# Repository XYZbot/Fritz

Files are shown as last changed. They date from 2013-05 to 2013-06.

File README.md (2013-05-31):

# Fritz : a robotic puppet

Fritz is an animatronic puppet that is controlled by an Arduino microcontroller. Fritz 
was created to provide an inexpensive introduction into robotics that is both entertaining, creative 
and educational. With an open source directive, Fritz is accompanied by a PC application to 
provide you with an easy to use interface in customizing and interacting with the project mechanics.

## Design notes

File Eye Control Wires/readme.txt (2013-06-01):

Open source release 1.0

Date: 5/31/2013

This directory contains .pdf files that show mechanical drawings
for how to make the control wires for Fritz.

These parts can be made using 0.032" diameter music wire.  Bends
can be made by hand using needle nose pliars.  A digital caliper
will be highly useful in making measurements prior to making bends.

There are 2 each of the horizontal and vertical wires.  There
are 4 each of the eyelid wires.

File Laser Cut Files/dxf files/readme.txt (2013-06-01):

Open source release 1.0

Date: 5/31/2013

This directory contains .dxf format files exported from solidworks.
These files can be used to import into a program to do laser cutting
of the parts for Fritz.

Note that parts that are repeated (occur more than once in a Fritz)
have a "_2x" in the filename to signal to you that you need more 
than one.

www.xyzbot.com

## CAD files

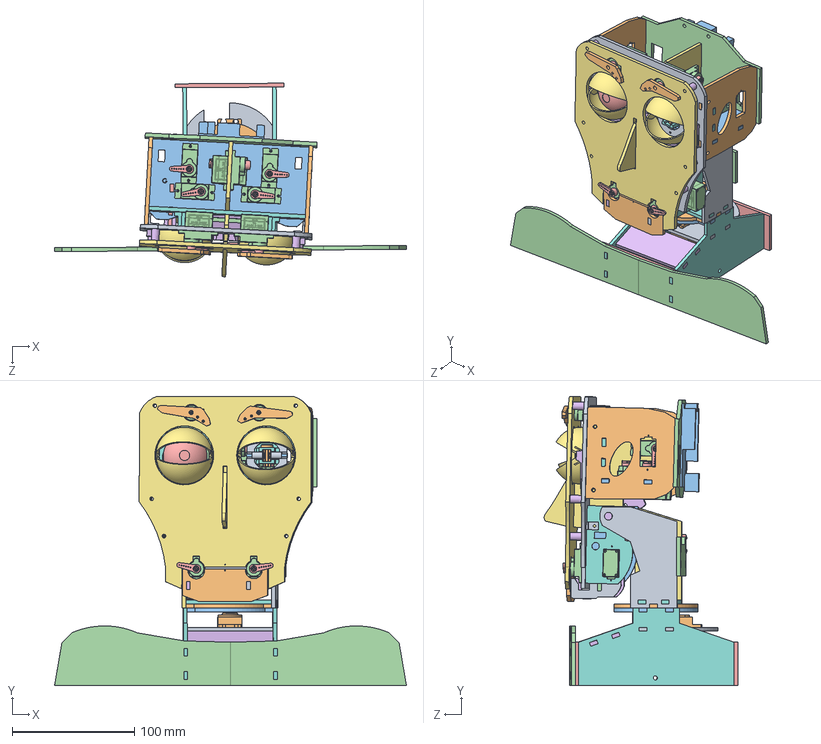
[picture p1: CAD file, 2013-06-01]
Solidworks Files/AssemblyFull.SLDASM
287.8 x 236.6 x 158.4 mm
faceFrameBack
skullbox_side x 2
skullbox_bottom
SG90 BODY x 11
SG90 ARM x 11
spacer_#6thread_3_4trlong x 6
faceFrameFront
skullBoxMandible
jawbone3
jawFront
skullBoxMandibleRight
jawCrossBeam
mandibleBack
jawboneRight
skullBoxNosePanel
skullbox_firewall
angleBracket_4_40screwThread x 6
eyebrow x 2
unoKitBoard
skullbox_back
gearLargeB
gearLargeNoTabs x 2
spacerNeckTilt
eyeBracket_straightPull x 2
eyeRing_straightPull x 2
clevisPin_cored x 2
eyeXAxisRod x 2
spacer_1_4trlong x 4
eye
eyeLidMount_B x 2
eyelidA x 4
rotateBaseSides x 2
rotateBaseServoPlate
Standard ServoB x 2
thrustBearingBottom
shoulderFront x 2
chestWall x 2
neckCover
neckTiltColumn
neckTiltColumnBottom
neckTiltColumnLeft
thrustBearingTop
servoHorn4Arm_standardSize
neckTiltColumnBack
gearSmall
tiltAxle

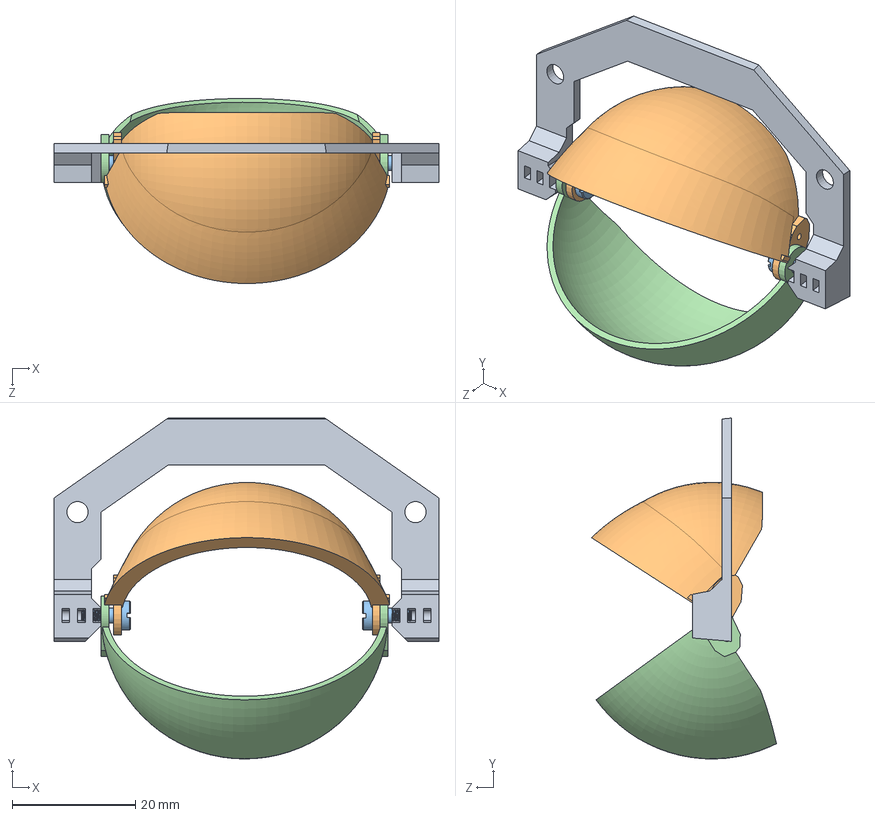
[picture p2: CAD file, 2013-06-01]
Solidworks Files/Assembly_EyeLid.SLDASM
62.4 x 55.2 x 30.0 mm
eyeLidMount_B
eyelidBottomD
shoulderScrew_2_56_1_8ths_shoulderLngth x 2
eyelidTopB

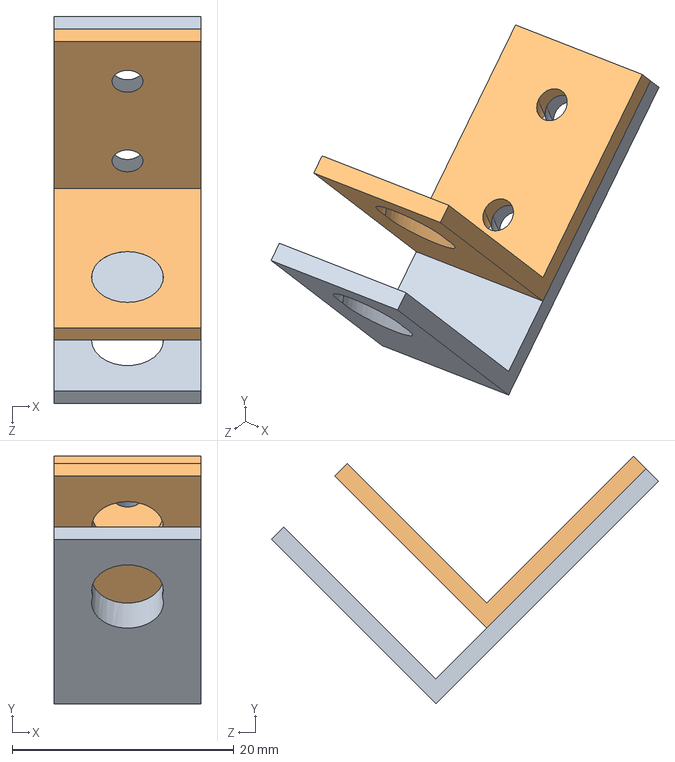
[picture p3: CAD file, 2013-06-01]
Solidworks Files/Assembly_eyeBracket.SLDASM
13.2 x 22.3 x 34.9 mm
eyeBracketHalf2
eyeBracketHalf1

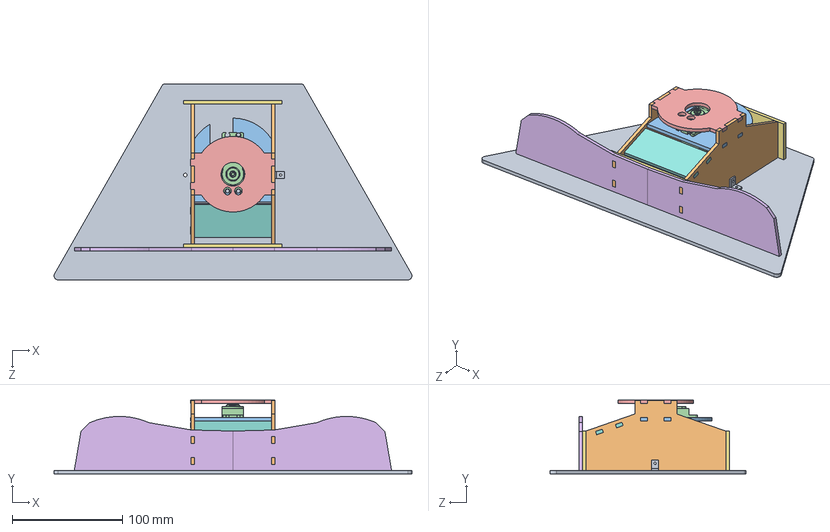
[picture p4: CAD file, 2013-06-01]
Solidworks Files/assemblyBaseToBasePlate.SLDASM
324.7 x 66.7 x 177.8 mm
basePlate
rotateBaseSides x 2
rotateBaseServoPlate
Standard ServoB
thrustBearingBottom
shoulderFront x 2
chestWall x 2
neckCover
angleBracket_4_40screwThread

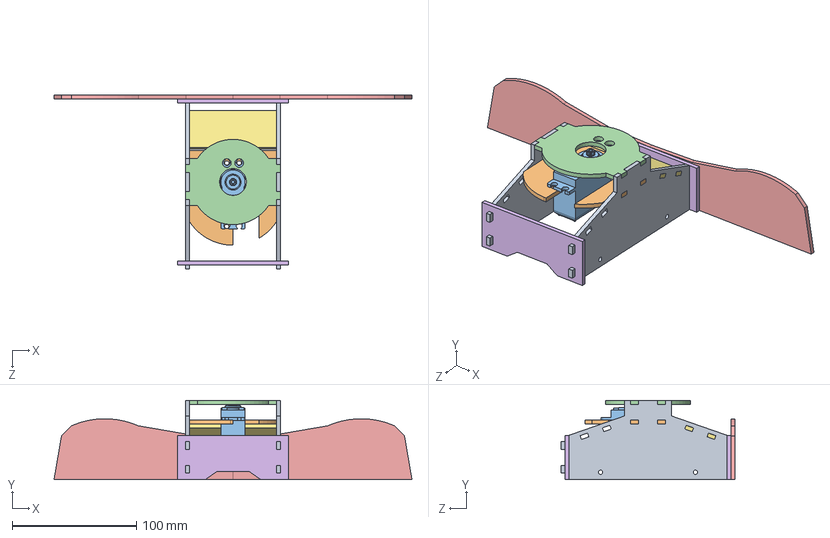
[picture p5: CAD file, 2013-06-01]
Solidworks Files/assemblyRotateBase.SLDASM
287.8 x 63.6 x 139.7 mm
rotateBaseSides x 2
rotateBaseServoPlate
Standard ServoB
thrustBearingBottom
shoulderFront x 2
chestWall x 2
neckCover

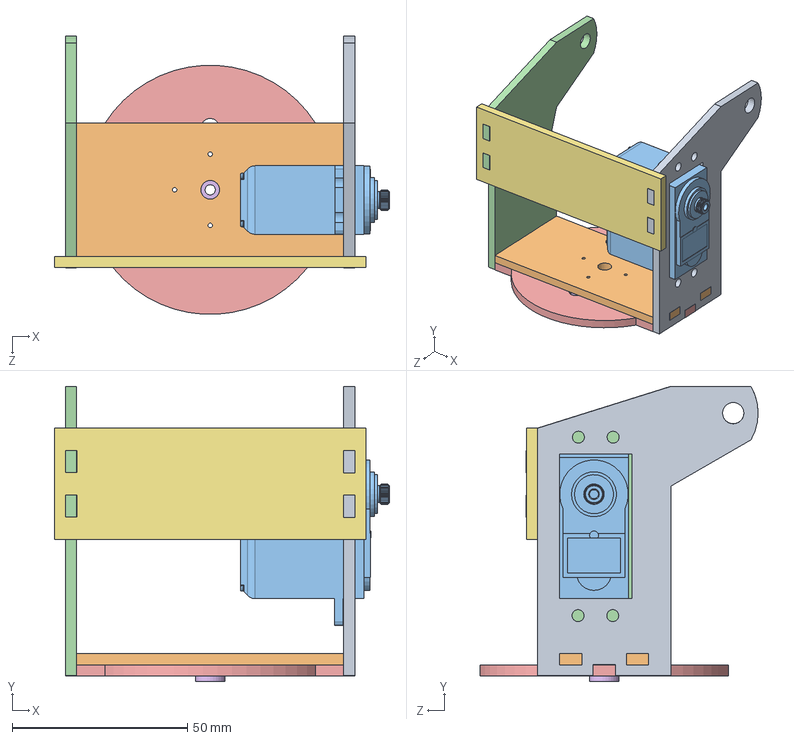
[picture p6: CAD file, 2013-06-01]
Solidworks Files/AssemblyNeckTiltColumn.SLDASM
95.6 x 84.3 x 79.4 mm
neckTiltColumn
neckTiltColumnBottom
Standard ServoB
neckTiltColumnLeft
thrustBearingTop
servoHorn4Arm_standardSize
neckTiltColumnBack

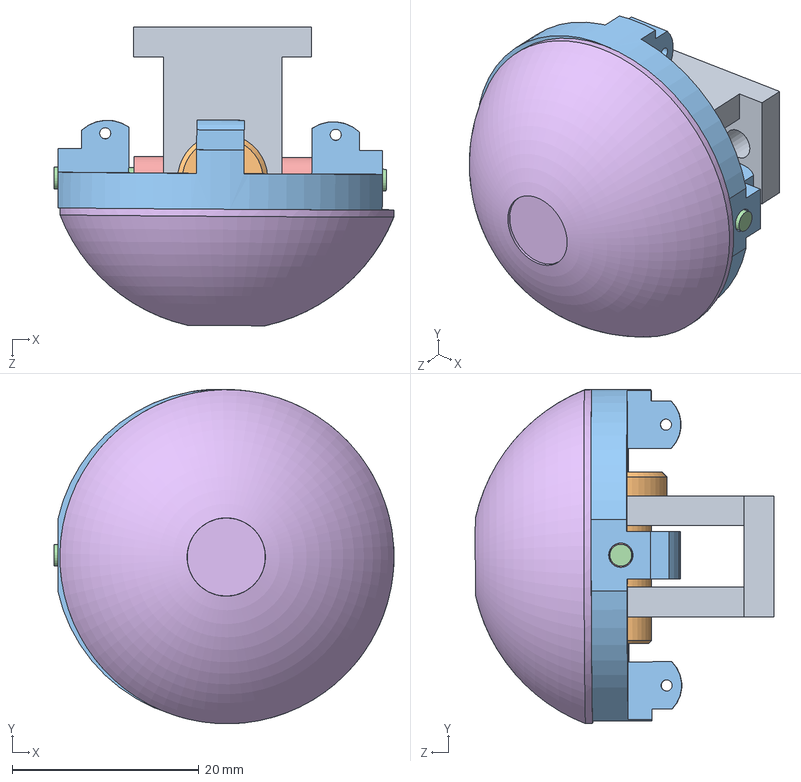
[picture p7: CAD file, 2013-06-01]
Solidworks Files/AssemblyEye.SLDASM
36.4 x 35.8 x 32.0 mm
uBracket
clevis_pin
eyeRingr4
eyeXAxisRod
spacer_1_4trlong x 2
eye

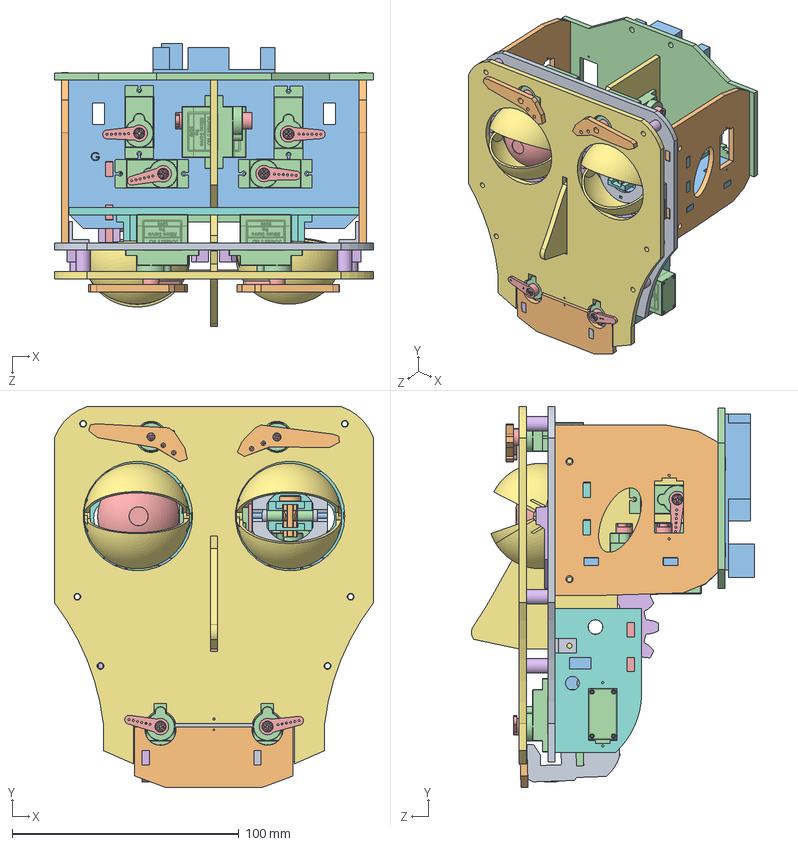
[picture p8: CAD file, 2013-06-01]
Solidworks Files/Assembly_skullbox.SLDASM
140.7 x 167.9 x 124.8 mm
faceFrameBack
skullbox_side x 2
skullbox_bottom
SG90 BODY x 11
SG90 ARM x 11
spacer_#6thread_3_4trlong x 6
faceFrameFront
skullBoxMandible
jawbone3
jawFront
skullBoxMandibleRight
jawCrossBeam
mandibleBack
jawboneRight
skullBoxNosePanel
skullbox_firewall
angleBracket_4_40screwThread x 6
eyebrow x 2
unoKitBoard
skullbox_back
gearLargeB
gearLargeNoTabs x 2
spacerNeckTilt
eyeBracket_straightPull x 2
eyeRing_straightPull x 2
clevisPin_cored x 2
eyeXAxisRod x 2
spacer_1_4trlong x 4
eye
eyeLidMount_B x 2
eyelidA x 4

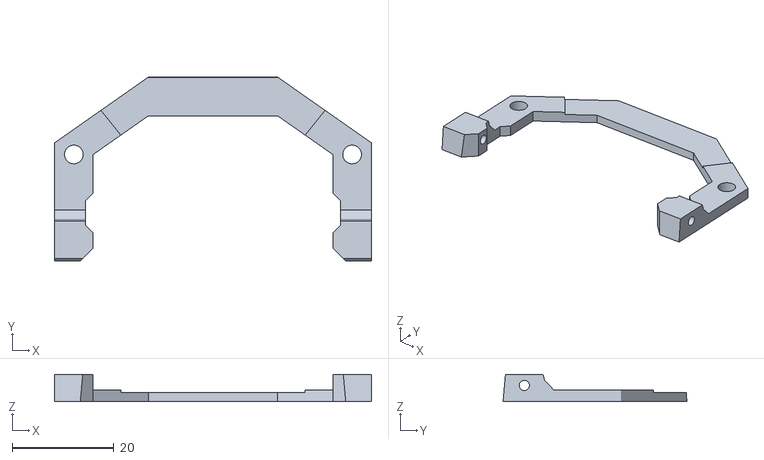
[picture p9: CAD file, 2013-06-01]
3D Printer Files/stl files/eyeLidMount_B.STL
62.4 x 36.2 x 5.33

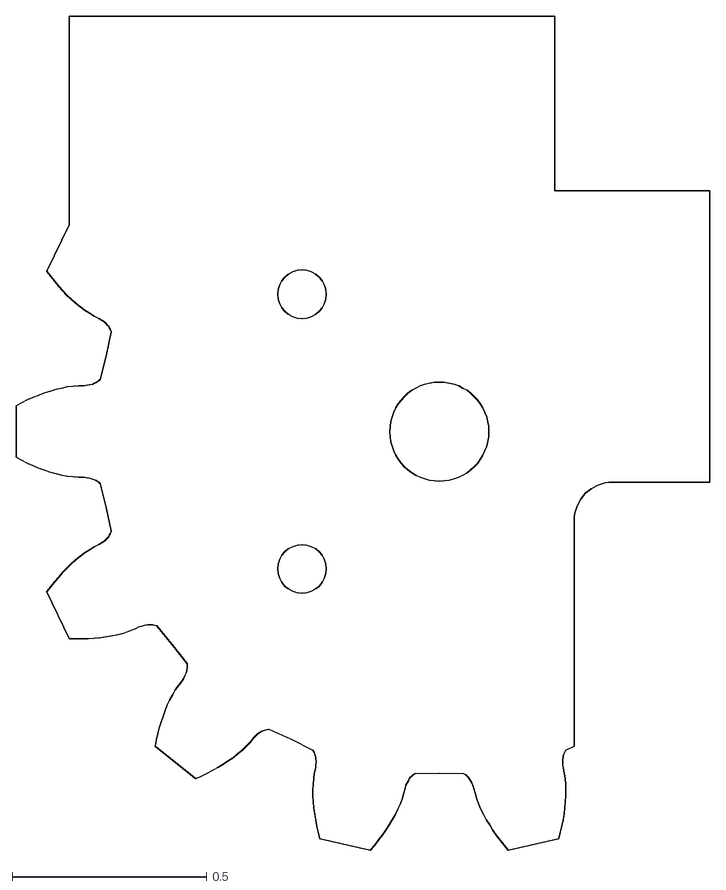
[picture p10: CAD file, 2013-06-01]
Laser Cut Files/dxf files/gearLargeNoTabs.DXF
1.79 x 2.15

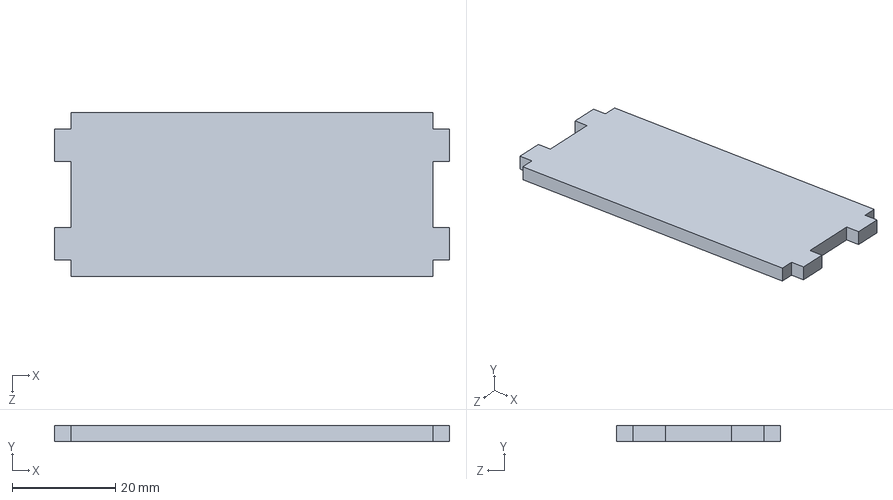
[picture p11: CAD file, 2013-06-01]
Solidworks Files/neckCover.SLDPRT
76.6 x 3.17 x 31.8 mm

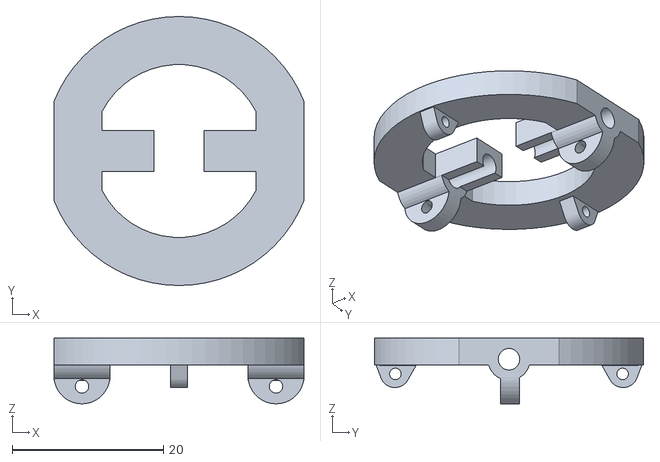
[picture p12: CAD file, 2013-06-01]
3D Printer Files/stl files/eyeRing_3D_rF.STL
33.0 x 35.6 x 8.70

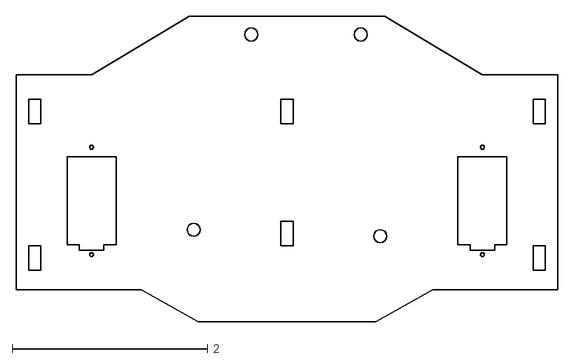
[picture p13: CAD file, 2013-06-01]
Laser Cut Files/dxf files/skullbox_back.DXF
5.54 x 3.13

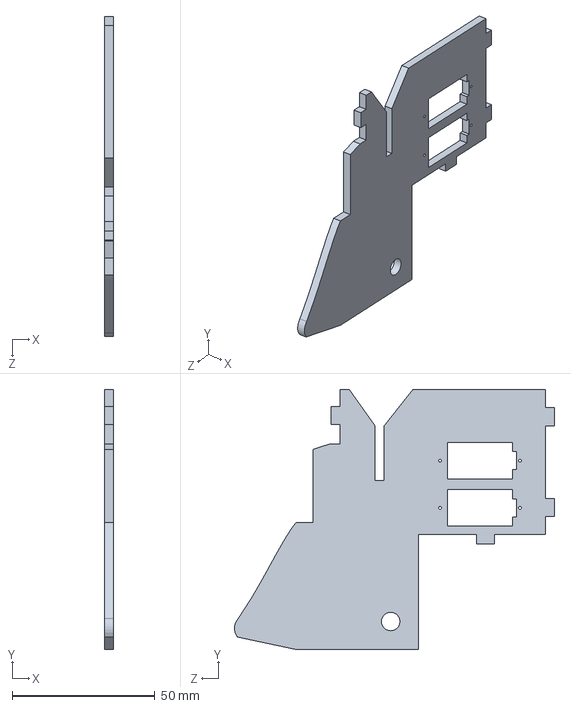
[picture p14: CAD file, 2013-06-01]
Solidworks Files/skullBoxNosePanel.SLDPRT
3.17 x 90.9 x 112.0 mm

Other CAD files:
3D Printer Files/stl files/eyelid3d_wButtress.STL
Laser Cut Files/dxf files/thrustBearingTop.DXF
Solidworks Files/neckRotateServoPlate.SLDPRT
3D Printer Files/stl files/eye bracket 3D-C.STL
3D Printer Files/stl files/clevisPin_3DPrint_B.STL
3D Printer Files/stl files/eyelid3DPrint.STL
Laser Cut Files/dxf files/basePlate.DXF
Laser Cut Files/dxf files/chestWall.DXF
Laser Cut Files/dxf files/eyebrow.DXF
Laser Cut Files/dxf files/faceFrameBack.DXF
Laser Cut Files/dxf files/faceFrameFront.DXF
Laser Cut Files/dxf files/faceFrameFront_devilHead.DXF
Laser Cut Files/dxf files/gearLargeB_2X.DXF
Laser Cut Files/dxf files/gearSmall.DXF
Laser Cut Files/dxf files/gearSmallForAcrylic1_8th.DXF
Laser Cut Files/dxf files/jawCrossBeam.DXF
Laser Cut Files/dxf files/jawFront.DXF
Laser Cut Files/dxf files/jawbone3.DXF
Laser Cut Files/dxf files/jawboneRight.DXF
Laser Cut Files/dxf files/mandibleBack.DXF
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

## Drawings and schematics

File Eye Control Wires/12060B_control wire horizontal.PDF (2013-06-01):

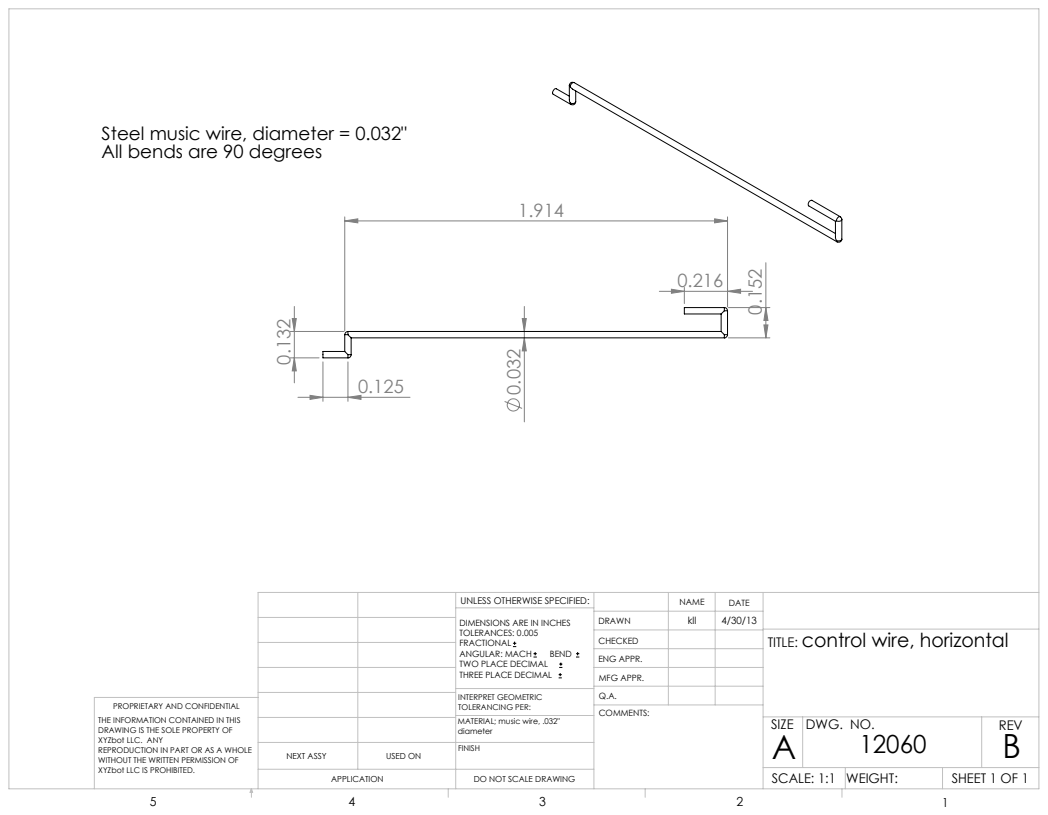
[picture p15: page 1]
SHEET 1 OF 1; SCALE: 1:1 WEIGHT:; DWG. NO.; REV; MFG APPR.; ENG APPR.; ANGULAR: MACH; BEND; NEXT ASSY; USED ON

Steel music wire, diameter = 0.032"
All bends are 90 degrees

UNLESS OTHERWISE SPECIFIED:

DIMENSIONS ARE IN INCHES
TOLERANCES: 0.005
FRACTIONAL
TWO PLACE DECIMAL
THREE PLACE DECIMAL

TITLE: control wire, horizontal

INTERPRET GEOMETRIC
TOLERANCING PER:
MATERIAL; music wire, .032"
diameter
FINISH

PROPRIETARY AND CONFIDENTIAL
THE INFORMATION CONTAINED IN THIS
DRAWING IS THE SOLE PROPERTY OF
XYZbot LLC. ANY
REPRODUCTION IN PART OR AS A WHOLE
WITHOUT THE WRITTEN PERMISSION OF
XYZbot LLC IS PROHIBITED.

DO NOT SCALE DRAWING

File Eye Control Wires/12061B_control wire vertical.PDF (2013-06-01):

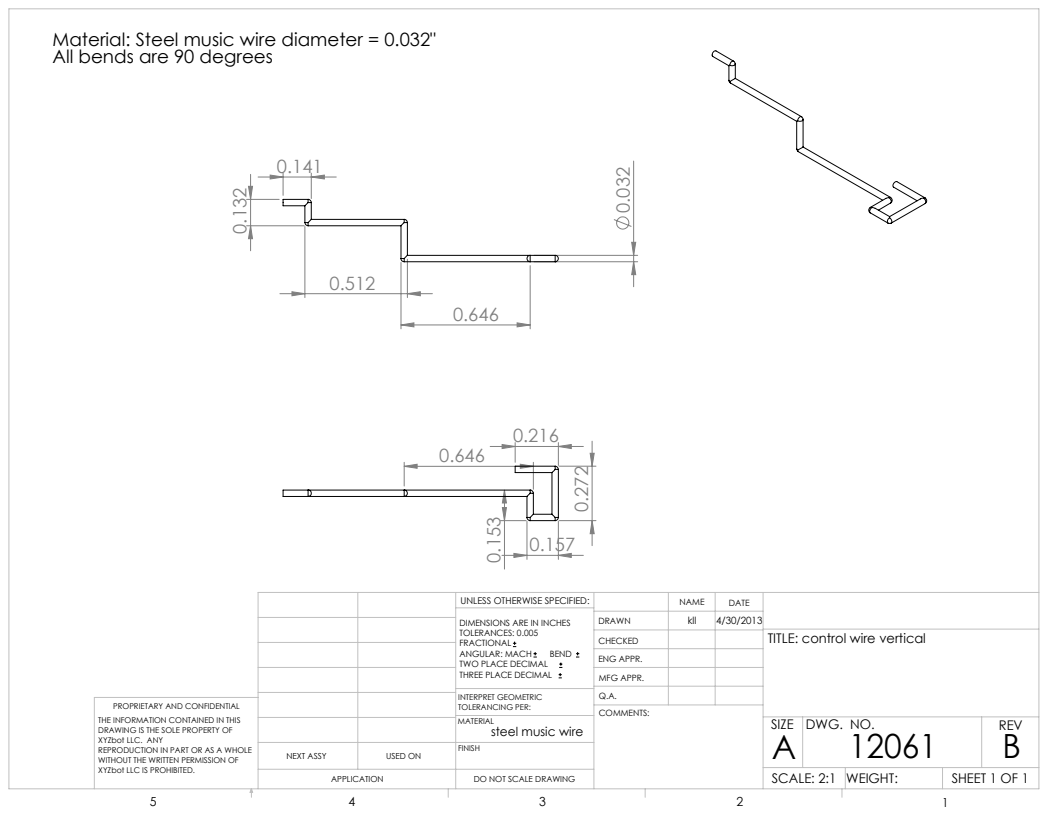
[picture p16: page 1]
SHEET 1 OF 1; SCALE: 2:1 WEIGHT:; DWG. NO.; REV; MFG APPR.; ENG APPR.; ANGULAR: MACH; BEND; NEXT ASSY; USED ON

Material: Steel music wire diameter = 0.032"
All bends are 90 degrees

UNLESS OTHERWISE SPECIFIED:

DIMENSIONS ARE IN INCHES
TOLERANCES: 0.005
FRACTIONAL
TWO PLACE DECIMAL
THREE PLACE DECIMAL

TITLE: control wire vertical

INTERPRET GEOMETRIC
TOLERANCING PER:
MATERIAL
steel music wire
FINISH

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

DO NOT SCALE DRAWING

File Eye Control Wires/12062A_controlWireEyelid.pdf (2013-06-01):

# Material: steel music wire, diameter = 0.032"

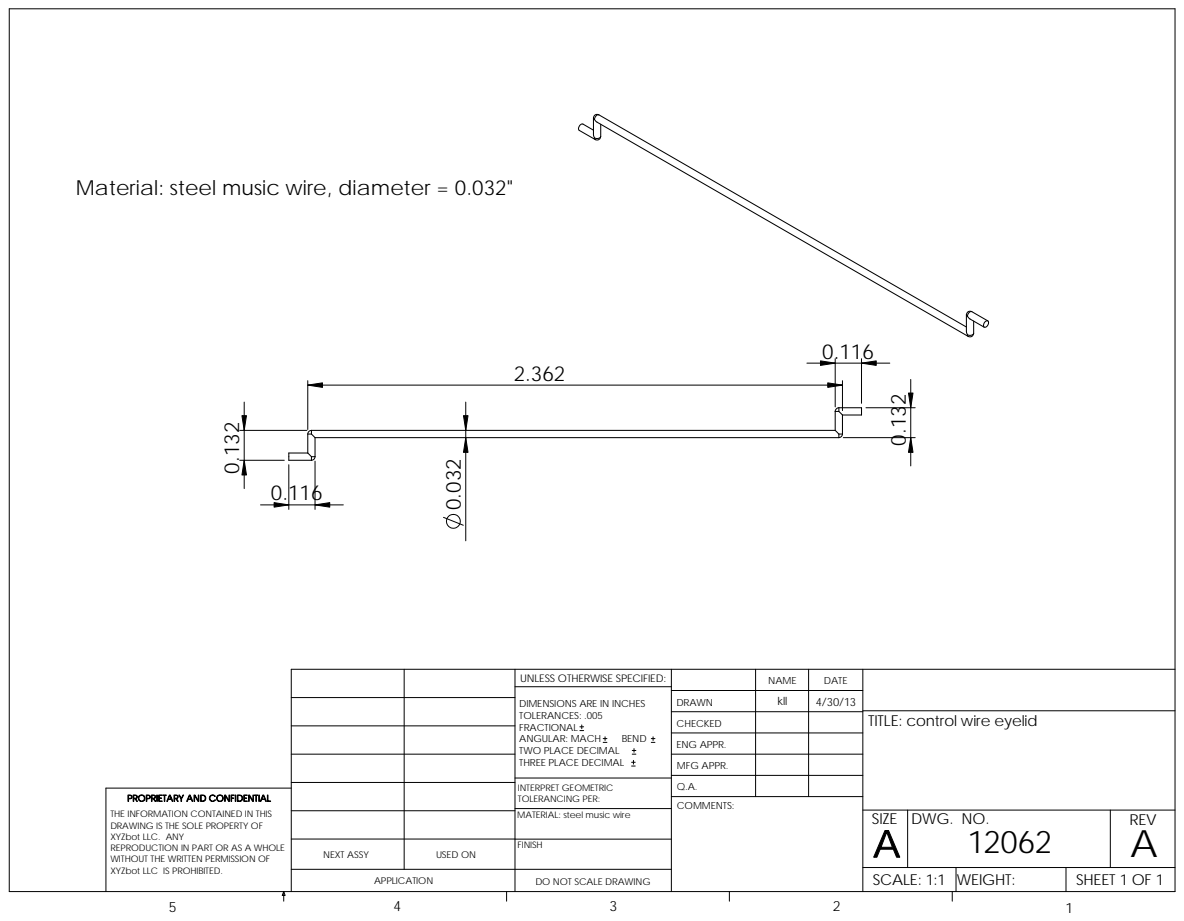
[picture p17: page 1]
COMMENTS:; BEND

UNLESS OTHERWISE SPECIFIED: | | NAME | DATE

DRAWN | kll | 4/30/13
CHECKED | | | TITLE: control wire eyelid

DIMENSIONS ARE IN INCHES
TOLERANCES: .005
FRACTIONAL
ANGULAR: MACH
TWO PLACE DECIMAL
THREE PLACE DECIMAL

ENG APPR.
MFG APPR.

INTERPRET GEOMETRIC TOLERANCING PER: | Q.A.
MATERIAL: steel music wire | | SIZE A | DWG. NO. 12062 | REV A

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

NEXT ASSY | USED ON | FINISH
APPLICATION | DO NOT SCALE DRAWING | | SCALE: 1:1 | WEIGHT: | SHEET 1 OF 1

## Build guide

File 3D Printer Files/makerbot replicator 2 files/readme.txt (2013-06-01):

Open source release 1.0

Date: 5/31/2013

This directory contains files for Makerbot Replicator 2.  The .thing files are just the 
geometry of the parts arranged near center of the table.

The .x3g files are printable binary files with all default settings except temperature is 
set at 235C (5C higher than default).  Resoution is medium.

www.xyzbot.com

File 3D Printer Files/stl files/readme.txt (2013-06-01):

Open source release 1.0

Date: 5/31/2013

This directory contains .stl format files for Fritz, the robotic head.

There are 2 versions of the eyelid.  One with buttresses, which is a built
in support. The other is the straight .stl file.  Users can use this 
to make their own supports, or have their machine autogenerate supports.  
Supports will be needed with this part.

All other .stl file parts do not need supports.

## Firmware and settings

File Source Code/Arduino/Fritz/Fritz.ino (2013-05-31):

#define MIN_PULSE_WIDTH       500     // the shortest pulse sent to a servo
#define MAX_PULSE_WIDTH      2500     // the longest pulse sent to a servo
#define REFRESH_INTERVAL    20000     // minumim time to refresh servos in microseconds

#define SERVOS_PER_BANK       10     // the maximum number of servos controlled by one timer bank
#define MAX_SERVOS   20				// the maximum number of possible servos to control on the UNO

#define INTERRUPT_OVERHEAD 2

#include <avr/interrupt.h>
#include <Arduino.h>

// identifies which servo pin is currently being pulsed
static volatile char ss_currentServo = -1;
static volatile unsigned char ss_pulseBank = 0;
static volatile int ss_pulseDiff = -1;
static volatile unsigned int ss_ServoTicks[MAX_SERVOS];
static volatile unsigned int ss_TurnOff[MAX_SERVOS];
static volatile unsigned int ss_refreshInterval;
static volatile unsigned int ss_bankClk;

/************ ISP (Interrupt Service Proceedure) ***********************/
SIGNAL (TIMER1_COMPA_vect)
{
  // if we are starting a new 20ms frame, initialize the timer counter to zero
  if(ss_currentServo < 0 )
    TCNT1 = 0;
  else
  {
    int index = ss_currentServo+ss_pulseBank;
    // stop the pulse on this servo if it is activated
    if(ss_ServoTicks[index] > 0)
    {
      digitalWrite(index, LOW);
      if (ss_TurnOff[index])
      {
        ss_ServoTicks[index]=0;
        ss_TurnOff[index]=0;
        pinMode(index, INPUT);
      }
    }    

    if (ss_pulseDiff == 0)
    {
      // stop the pulse on this servo if it is activated
      int index = ss_currentServo+(ss_pulseBank^SERVOS_PER_BANK);
      if(ss_ServoTicks[index] > 0)
      {
        digitalWrite(index, LOW);
        if (ss_TurnOff[index])
        {
          ss_ServoTicks[index]=0;
          ss_TurnOff[index]=0;
          pinMode(index, INPUT);
        }
      }
    }
    else
    // if we need to wait for the sibling pulse to trigger do so
    if (ss_pulseDiff == 1)
    {
      // if we ran out of time ... stop the second pulse
      if (((unsigned)TCNT1)>(ss_bankClk+4))
      {
        int index = ss_currentServo+(ss_pulseBank^SERVOS_PER_BANK);
        // stop the pulse on this servo if it is activated
        if(ss_ServoTicks[index] > 0)
        {
          digitalWrite(index, LOW);
          if (ss_TurnOff[index])
          {
            ss_ServoTicks[index]=0;
            ss_TurnOff[index]=0;
            pinMode(index, INPUT);
          }
        }
      }
      else
      {
        // setup timer callback
        OCR1A = ss_bankClk;

        // indicate we are done with both servos
        ss_pulseDiff = -1;

        // switch to the other servo bank
        ss_pulseBank ^=SERVOS_PER_BANK;

        return;
      }
    }
  }

  // increment to the next pin
  if ((++ss_currentServo) < SERVOS_PER_BANK)
  {
    // keep track of which pulse is longer, bank0 or bank1
    unsigned int bankClk = 0;
    unsigned int altBankClk = 0;

    ss_pulseDiff = -1;
    ss_pulseBank = 0;

    int val = ss_ServoTicks[ss_currentServo];
    // setup to callback this function after the pulse size of the current servo
    if (val > 0)
    {
      // start the pulse
      digitalWrite(ss_currentServo, HIGH);

      bankClk = ((unsigned)TCNT1) + val;
    }

    int secondCurrentServo = ss_currentServo+SERVOS_PER_BANK;
    val = ss_ServoTicks[secondCurrentServo];
    if (val > 0)
    {
      // start the second pulse
      digitalWrite(secondCurrentServo, HIGH);

      altBankClk = ((unsigned)TCNT1)+val;

      // if this pulse is shorter than the first use it!
      if ((altBankClk<bankClk)||(bankClk==0))
      {
        // save the difference between the pulse sizes
        ss_pulseDiff = 1;

        ss_bankClk = bankClk;

        bankClk = altBankClk;

        // remember that we are referring to the second bank
        ss_pulseBank = SERVOS_PER_BANK;

      }
      else
      {
        ss_bankClk = altBankClk;

        if (altBankClk==bankClk)
          ss_pulseDiff = 0;
        else
          ss_pulseDiff = 1;
      }
    }

    if (bankClk > (((unsigned)TCNT1)+ INTERRUPT_OVERHEAD))
      OCR1A = bankClk - INTERRUPT_OVERHEAD;
    else
      OCR1A = ((unsigned)TCNT1) + 4;
  }
  else
  {
    // we finished servicing all servos so wait to complete the 20ms period before starting over
    // the - 4 is to ensure that we are not about to miss a OCR interrupt
    if ((unsigned)TCNT1 <  (ss_refreshInterval - 4))
      OCR1A = ss_refreshInterval;
    else
      // for whatever reason, we've exceeded the 20ms time period ... just setup to call back asap
      OCR1A = ((unsigned)TCNT1) + 4;

    // indicate that we are done with this period and to start a new one on the next callback
    ss_currentServo = -1;
  }
}

/****************** end of static functions ******************************/

void ss_Init()
{
  int i;
  for (i=0;i<MAX_SERVOS;i++)
  {
    ss_ServoTicks[i] = 0;
    ss_TurnOff[i] = 0;
  }
  
  TCCR1A = 0;             // normal counting mode
  TCCR1B = _BV(CS11);     // set prescaler of 8
  TCNT1 = 0;              // clear the timer count

  TIFR1 |= _BV(OCF1A);     // clear any pending interrupts;
  TIMSK1 |=  _BV(OCIE1A) ; // enable the output compare interrupt

  // cache the REFRESH_INTERVAL value in ticks instead of microseconds
  ss_refreshInterval = ((clockCyclesPerMicrosecond() * REFRESH_INTERVAL)>>3);
}

void ss_Destroy()
{
  // disable timer 1 output compare interrupt
  TIMSK1 &=  ~_BV(OCIE1A) ;
}

int ss_SetPosition(int pin, int value)
{
  // check that we have a valid pin (note that 0 and 1 are used for serial!)
  if ((pin<0)||(pin>=MAX_SERVOS)) return 0;

  // an out of bounds value indicates a servo shutdown
  if ((value < MIN_PULSE_WIDTH)||(value> MAX_PULSE_WIDTH))
  {
    if (ss_ServoTicks[pin]>0)
      ss_TurnOff[pin] = 1;
      
    return 0;
  }

  // convert from microseconds to clock ticks assuming prescaler of 8
  value = ((clockCyclesPerMicrosecond() * (value - INTERRUPT_OVERHEAD))>>3);

  // check that pin has been initialized
  int hold = ss_ServoTicks[pin];

  //unsigned char oldSREG = SREG;
  //cli();
  ss_ServoTicks[pin] = value;
  //SREG = oldSREG;

  // if value was zero, the pin had not been set to OUTPUT
  if (hold == 0)
  {
    // set servo pin to output
    pinMode( pin, OUTPUT);
  }
}

//////////////

#include <EEPROM.h>

int highestPin = 20;

unsigned char g_message[256];
unsigned char g_config[256];

unsigned int g_messageTop;
unsigned int g_command;
unsigned int g_length;
unsigned int g_crc;
unsigned int g_count;
unsigned int g_channel;
unsigned int g_value;
long g_calc;

unsigned long g_heartBeat[20];

#define ARDUINO_GET_ID 0
#define ARDUINO_RESET 1
#define ARDUINO_SET_OBJECT 2
#define ARDUINO_SET_SERVO 3
#define ARDUINO_HEARTBEAT 4
#define ARDUINO_RELEASE_SERVO 5
#define ARDUINO_GET_IR 6
#define ARDUINO_GET_SONAR 7

#define ARDUINO_LOAD 32
#define ARDUINO_SAVE 33

#define MAX_CONFIG (65*2)

void initialize()
{
  int i;
  for (i=0;i<highestPin;i++) g_heartBeat[i]=(long)0;
  
  for (i=0;i<MAX_CONFIG;i++)
    g_config[i]=EEPROM.read(i);
}

void setup()
{
  Serial.begin(57600);

  ss_Init();
}

int readPacket()
{
  // get header byte
  // 128 (bit 8) flag indicates a new g_command packet ..
  //		that means the g_value bytes can never have 128 set!
  // next byte is the g_command 0-8
  // next byte is single byte data length
  // for command >= 32 next byte is high byte data length
  // data
  // crc

  int high;
  int crc;
  g_messageTop=2;

  do
  {
    while (Serial.available() <= 0) continue;
    g_command = Serial.read();
  }
  while ((g_command&128)==0);

  g_message[0] = crc = g_command;
  g_command^=128;

  while (Serial.available() <= 0) continue;
  g_length = g_message[1] = Serial.read();
  crc ^= g_length;

  if (g_command>=32)
  {
    while (Serial.available() <= 0) continue;
    g_message[2] = high = Serial.read();
    g_length = g_length|(high<<7);
    crc ^= high;
    g_messageTop=3;
  }

  // read in entire message
  if (g_length>0)
  {
    int count = g_length;
    while (count>0)
    {
      while (Serial.available() <= 0) continue;
      g_message[g_messageTop] = Serial.read();
      crc ^= g_message[g_messageTop++];
      count--;
    }

    while (Serial.available() <= 0) continue;
    g_message[g_messageTop++] = g_crc = Serial.read();

    if ((crc&127)!=(g_crc&127)) return 0;
  }
  return 1;
}

void echoPacket()
{
  Serial.write(g_message, g_messageTop);
}

void loop()
{
  //ss_SetPosition(4, 1500);
  //return;
/*
  int p, q;
  for (p=700, q=800;p<2300;p++, q++)
  {
    //ss_SetPosition(14, p);
    ss_SetPosition(19, q);
    delay(5);
  }

  for (;p>=700;p--,q--)
  {
    //ss_SetPosition(14, p);
    ss_SetPosition(19, q);
    delay(5);
  }
  return;
*/

  int crc;
  int val;
  int i,j;
  int trimVal, maxVal, minVal, pin;

  while (Serial.available()>0)
  {
    if (readPacket()==0) 
      return;

    switch (g_command)
    {
      // init
      case  ARDUINO_GET_ID:
        initialize();
        Serial.print("ARDU004");
      break;
      // servo
      case  ARDUINO_RELEASE_SERVO:
        g_channel = g_message[2];
        ss_SetPosition(g_channel, 0);
        echoPacket();
      break;
      case  ARDUINO_SET_SERVO:
        g_channel = g_message[2];
        g_value = g_message[3] | (g_message[4]<<7);

        ss_SetPosition(g_channel, g_value);

        g_heartBeat[g_channel]=millis();

        echoPacket();
      break;
      case ARDUINO_SET_OBJECT:
        // sets the value of a specific part of the face. This uses configuration
        // memory to determine the pin and appropriate scaled min/max values.
        g_channel = g_message[2];
        val = g_message[3] | (g_message[4]<<7);
        if (val > 8192) val -= 16384;

        i = g_channel*10;
        
        trimVal = g_config[i] | (g_config[i+1]<<7);
        if (trimVal > 8192) trimVal -= 16384;
        maxVal = g_config[i+2] | (g_config[i+3]<<7);
        if (maxVal > 8192) maxVal -= 16384;
        minVal = g_config[i+4] | (g_config[i+5]<<7);
        if (minVal > 8192) minVal -= 16384;

        pin = g_config[i+6] | (g_config[i+7]<<7);

        if (pin!=0)
        {
          g_calc = (((long)val+1000)* ((long)(maxVal - minVal)))/(long)2000;
          
          val = g_calc + trimVal + minVal;
          if (val<-1000) val=-1000;
          if (val>1000) val=1000;
          if (val<minVal) val=minVal;
          if (val>maxVal) val=maxVal;
          ss_SetPosition(pin, val+1500);
          g_heartBeat[pin]=millis();
        }
        
        echoPacket();
      break;
      case ARDUINO_HEARTBEAT:
      break;
      case ARDUINO_LOAD:
        g_count = g_message[3]*2;

        g_message[0]=g_command|128;
        g_message[1]=g_count+1;
        g_message[2]=0;

        crc=g_message[0]^g_message[1]^g_message[2];

	for (j=3,i=0;i<g_count;i+=2,j+=2)
	{
	  g_message[j] = g_config[i];
	  g_message[j+1] = g_config[i+1];
	  crc=crc^g_message[j]^g_message[j+1];
	}
	g_message[j]=crc&127;

	for (i=3;i<j;i+=10)
        {
           trimVal = g_message[i] | (g_message[i+1]<<7);
           if (trimVal > 8192) trimVal -= 16384;
           maxVal = g_message[i+2] | (g_message[i+3]<<7);
           if (maxVal > 8192) maxVal -= 16384;
           minVal = g_message[i+4] | (g_message[i+5]<<7);
           if (minVal > 8192) minVal -= 16384;
           pin = g_message[i+6] | (g_message[i+7]<<7);

          if (pin!=0)
          {
            val = ((maxVal-minVal)/2)+minVal+trimVal;
            if (val<-1000) val=-1000;
            if (val>1000) val=1000;
            if (val<minVal) val=minVal;
            if (val>maxVal) val=maxVal;
            ss_SetPosition(pin, val+1500);
           g_heartBeat[pin]=millis();
          }
        }

	Serial.write(g_message, j+1);

      break;
      case ARDUINO_SAVE:

	for (j=3,i=0;i<g_length;i+=2,j+=2)
	{
          EEPROM.write(i, g_message[j]);
          g_config[i] = g_message[j];
          EEPROM.write(i+1, g_message[j+1]);
          g_config[i+1] = g_message[j+1];
        }

        g_message[0]=g_command|128;
        g_message[1]=0;
        g_message[2]=0;
	Serial.write(g_message, 3);
      break;
      case ARDUINO_RESET:

	for (i=0;i<MAX_CONFIG;i+=10)
        {
           trimVal = g_config[i] | (g_config[i+1]<<7);
           if (trimVal > 8192) trimVal -= 16384;
           maxVal = g_config[i+2] | (g_config[i+3]<<7);
           if (maxVal > 8192) maxVal -= 16384;
           minVal = g_config[i+4] | (g_config[i+5]<<7);
           if (minVal > 8192) minVal -= 16384;
           pin = g_config[i+6] | (g_config[i+7]<<7);

          if (pin!=0)
          {
            val = ((maxVal-minVal)/2)+minVal+trimVal;
            if (val<-1000) val=-1000;
            if (val>1000) val=1000;
            if (val<minVal) val=minVal;
            if (val>maxVal) val=maxVal;
            ss_SetPosition(pin, val+1500);
            g_heartBeat[pin]=millis();
          }
        }

      break;
      case ARDUINO_GET_IR:
        g_channel = g_message[2];
        
        g_value = analogRead(g_channel);

        g_message[3] = g_value&127;
        g_message[4] = (g_value>>7)&127;

        echoPacket();

      break;
      case ARDUINO_GET_SONAR:
        digitalWrite(g_message[2], LOW);
        delayMicroseconds(2);
        digitalWrite(g_message[2], HIGH);
        delayMicroseconds(10); // Added this line
        digitalWrite(g_message[2], LOW);

        g_value = pulseIn(g_message[3], HIGH);
  
        g_message[3] = g_value&127;
        g_message[4] = (g_value>>7)&127;

        echoPacket();
      break;
    }
  }

  long sec = millis();
  for (i=0;i<highestPin;i++)
  {
    if (g_heartBeat[i]!=0)
    {
      if ((sec - g_heartBeat[i])>2000)
      {
        ss_SetPosition(i, 0);
        g_heartBeat[i]=0;
      }
    }
  }
}
